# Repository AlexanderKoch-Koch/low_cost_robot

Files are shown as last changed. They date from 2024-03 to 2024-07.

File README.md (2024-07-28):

# Low-Cost Robot Arm
Join the waitlist here to get all the parts in one package: https://tau-robotics.com/robots

This repository contains the files to build and control a low-cost robot arm that costs about $250. You can also build a second robot arm (the leader arm) to control the other arm (the follower arm) that costs about $180, for a total of $430. The design of the leader is inspired by the [GELLO project](https://github.com/wuphilipp/gello_mechanical) but is simpler to build. Such a robot arm is well suited for [robot learning](https://x.com/alexkoch_ai/status/1756500716854841835?s=20). Two of those arms are also capable of [folding clothes](https://x.com/alexkoch_ai/status/1772750496174149708?s=20).

This robot arm uses Dynamixel XL430 and Dynamixel XL330 servo motors. The XL430 motors are almost twice as strong and are used for the first two joints.
The XL330 motors are weaker but weigh only 18g each. This makes the arm very lightweight and fast.
Dynamixel sells the U2D2 adapter to connect the servos to a computer. However, this is very expensive and the latency is very high. This build uses another cheaper adapter board instead.
The robot arm can be controlled with the Dynamixel SDK: ```pip install dynamixel-sdk```

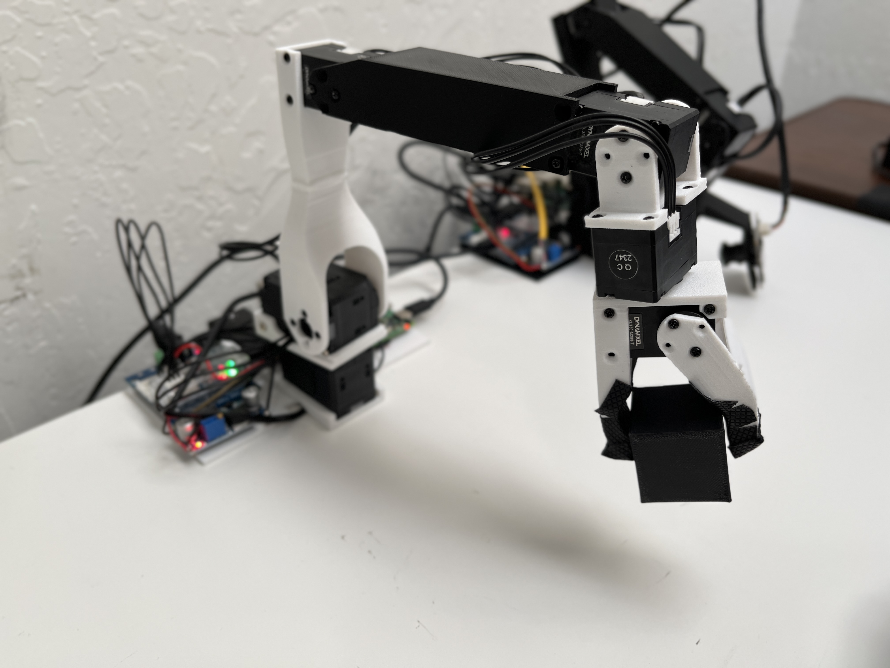
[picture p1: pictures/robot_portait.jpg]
Robot Arm


## Follower Arm

### Required Materials

| Part | Cost | Buying link | Specs |
|---|---|---| --- |
| 2x Dynamixel XL430-W250 | $100 | https://www.robotis.us/dynamixel-xl430-w250-t/ | https://emanual.robotis.com/docs/en/dxl/x/xl430-w250/ |
| 4x Dynamixel XL330-M288 | $96  | https://www.robotis.us/dynamixel-xl330-m288-t/ | https://emanual.robotis.com/docs/en/dxl/x/xl330-m288/|
| XL330 Idler Wheel | $10  | https://www.robotis.us/fpx330-h101-4pcs-set/ | **Note**: pack of four; three needed for  longer version pictured above (with elbow-to-wrist extension), two needed for shorter version shown in the [assembly video](https://youtu.be/RckrXOEoWrk)|
| XL430 Idler Wheel | $7 | https://www.robotis.us/hn11-i101-set/ | |
| Waveshare Serial Bus Servo Driver Board | $10  | https://a.co/d/7C3RUYU | |
| Voltage Reducer | $10 | https://a.co/d/cy02ADW | **Note**: pack of six, only one needed per follower arm |
| 12V Power Supply | $12  | https://a.co/d/40o8uMN | |
| Table Clamp | $6 | https://a.co/d/4KEiYdV | |
| Wires | $7 | https://a.co/d/hQfk2cb | |
| Total | $258 | | |

There is usually a 10% discount code for the Robotis shop. It might also help to add some grip tape to the gripper (e.g. https://a.co/d/dW7BnEN). A USB-C cable is necessary to connect the servo driver board to a computer.

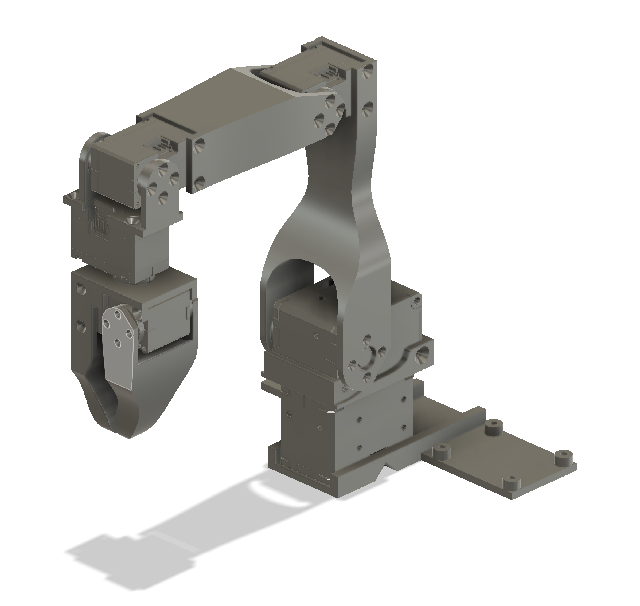
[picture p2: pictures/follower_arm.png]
follower


### Assembly

Video of the assembly: https://youtu.be/RckrXOEoWrk

1. Print all parts with a 3D printer
   1. The STL files are in `hardware/follower/stl`
   2. The parts are designed to be easy to print; only the moving part of the gripper needs supports
2. Scanning motors
   1. Connect the driver board to a computer (should work with Linux and MacOS)
   2. Figure out the device name (e.g. tty.usbmodem57380045631 for MacOS): ```ls /dev/tty.*```
   3. Scan each motor individually with [Dynamixel Wizard](https://emanual.robotis.com/docs/en/software/dynamixel/dynamixel_wizard2/)
      1. Set the baudrate to 1M for all motors
      2. Set the servo IDs to 1 for the shoulder to 5 (6 if using the elbow-to-wrist extension) for the gripper servo
3. Assembly
   1. Assemble the arm without the base
      1. Make sure that the servos are fixed in the same position as in the CAD
      2. The servo horn should be in the default position when screwed in
   2. Solder wires onto voltage reducer; input should be connected to female connectors and the output to male connectors
   3. Screw the voltage reducer and the servo driver board onto the base
   4. Screw the base onto the arm
   5. Connect D, V, and G ports on the driver board to the shoulder rotation servo
   6. Connect the shoulder rotation servo to the shoulder lift servo
   7. Connect the input for the voltage reducer to V and G ports on the driver board
   8. Connect the output of the voltage reducer and the remaining D port of the driver board to the elbow servo
   9. Connect the driver board to the power supply
   10. Connect to an XL330 servo and view the input voltage on Dynamixel Wizard, then adjust the screw on the voltage reducer until the input voltage is 5V

## Leader Arm

### Required Materials

| Part | Cost | Buying link | Specs |
|---|---| --- | --- |
| 6x Dynamixel XL330-M077 | $144 |  https://www.robotis.us/dynamixel-xl330-m077-t/ | https://emanual.robotis.com/docs/en/dxl/x/xl330-m077/|
| XL330 Frame | $7 | https://www.robotis.us/fpx330-s101-4pcs-set/ | |
| XL330 Idler Wheel | $10  | https://www.robotis.us/fpx330-h101-4pcs-set/ | **Note**: pack of four; three needed for longer version (with elbow-to-wrist extension), two needed for shorter version pictured below |
| Waveshare Serial Bus Servo Driver Board | $10  | https://a.co/d/7C3RUYU | |
| 5V Power Supply | $6 | https://a.co/d/5u90NVp | |
| Table Clamp | $6 | https://a.co/d/4KEiYdV | |
| Total | $183 | | |

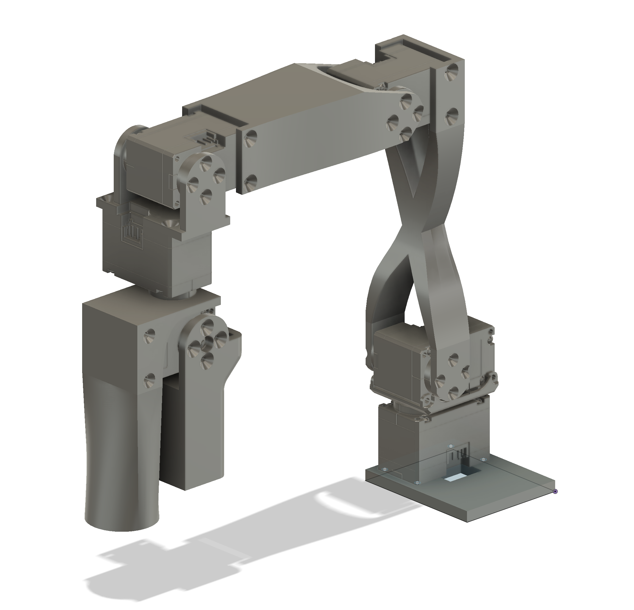
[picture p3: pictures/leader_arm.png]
leader


### Assembly

The assembly of the leader arm is simpler since all motors use 5V. The gripper is replace by a handle and a trigger. During use, a small torque can be applied to the trigger so that it opens by default. The GELLO design uses a spring for this purpose but it is much more difficult to assemble.
The `teleoperation.py` script can be used to test the arms. However, the device names might have to be adjusted.

## Simulation
A basic simulation environment in MuJoCo is available by running `simulation.py`.

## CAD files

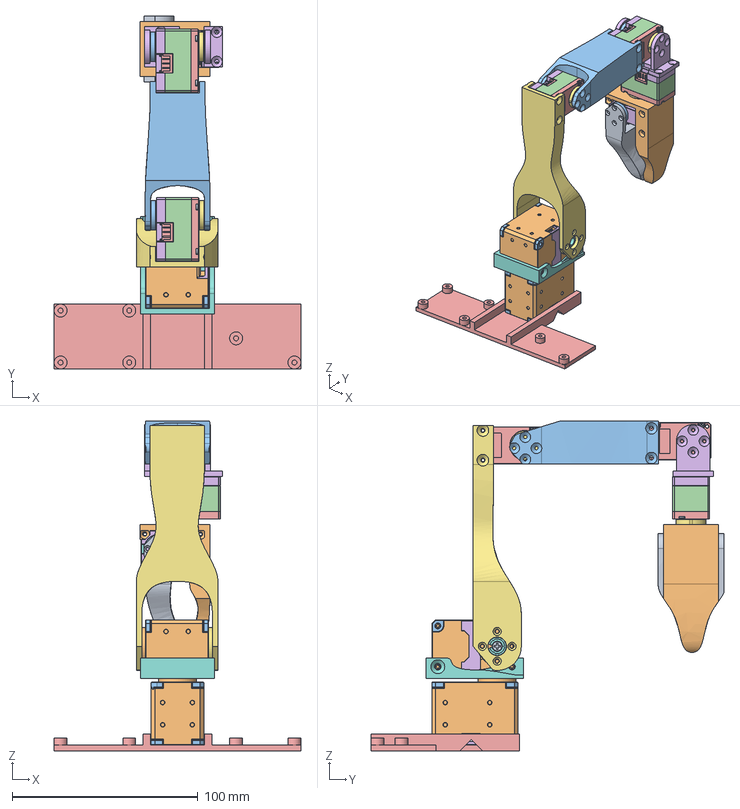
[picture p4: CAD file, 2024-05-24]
hardware/follower/step/arm.step
133.0 x 190.2 x 177.6 mm
DC11_A01_DUMMY x 2
DX124_SCREW-COVER x 2
B3B-EH x 4
DC11_A01_CASE_CVR_DUMMY x 2
DC11_A01_IDLER_DUMMY x 2
DC11_A01_IDLER_CAP_DUMMY x 2
DC11_A01_IDLER_SCREW x 2
FHS_M2_5X10 x 16
DC11_A01_SPACER_DUMMY x 16
DC15_A01_CASE_M_DUMMY x 4
DC15_A01_CASE_F_DUMMY x 4
DC15_A01_CASE_B_DUMMY x 4
DC15_A01_HORN_DUMMY x 4
DC15_A01_LED_CAP2_DUMMY x 4
PHS_1_7X20_5_DC10 x 16
BTS2_M2_6X8 x 8
DC15_A01_HORN_IDLE2_DUMMY x 4
DC15_A01_IDLE_CAP_DUMMY x 4
B3B-EH_1 x 8
Base
shoulder_rotation
connector
rotation connector
moving side
static side
connector_1

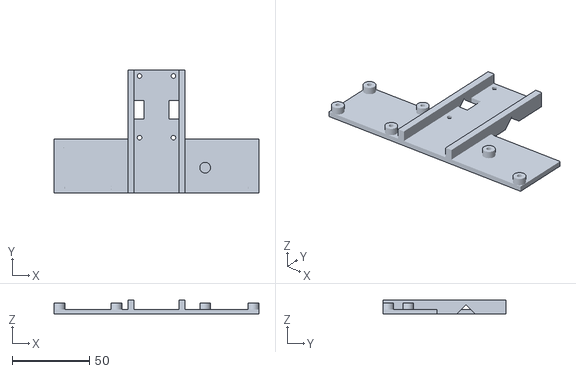
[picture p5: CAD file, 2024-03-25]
hardware/follower/stl/base.stl
133.0 x 80.0 x 9.00

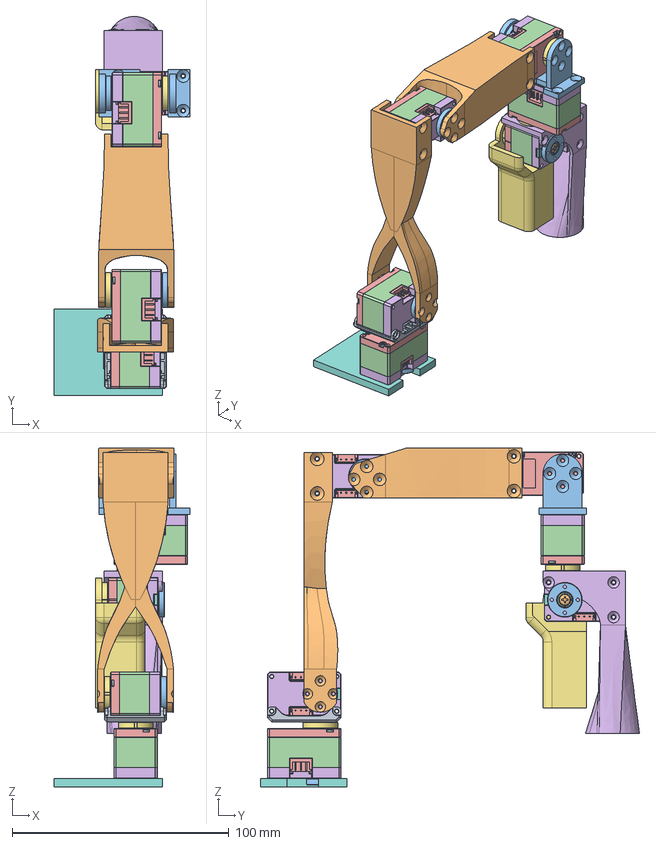
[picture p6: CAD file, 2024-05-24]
hardware/leader/step/leader_arm.step
62.7 x 175.0 x 156.5 mm
Servo Connector redesign
shoulder_rotation
DC15_A01_CASE_M_DUMMY x 6
DC15_A01_CASE_F_DUMMY x 6
DC15_A01_CASE_B_DUMMY x 6
DC15_A01_HORN_DUMMY x 6
DC15_A01_LED_CAP2_DUMMY x 6
PHS_1_7X20_5_DC10 x 24
BTS2_M2_6X8 x 12
DC15_A01_HORN_IDLE2_DUMMY x 6
DC15_A01_IDLE_CAP_DUMMY x 6
B3B-EH x 12
handle
trigger
base
fpx330-s101
connector

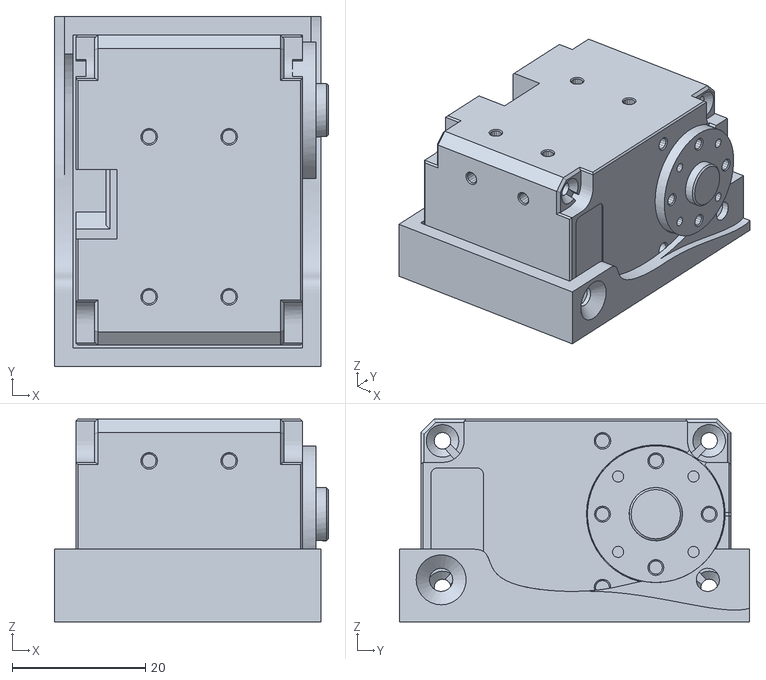
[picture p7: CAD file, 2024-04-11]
simulation/low_cost_robot/assets/first-bracket-motor_1.stl
41.1 x 52.5 x 30.4

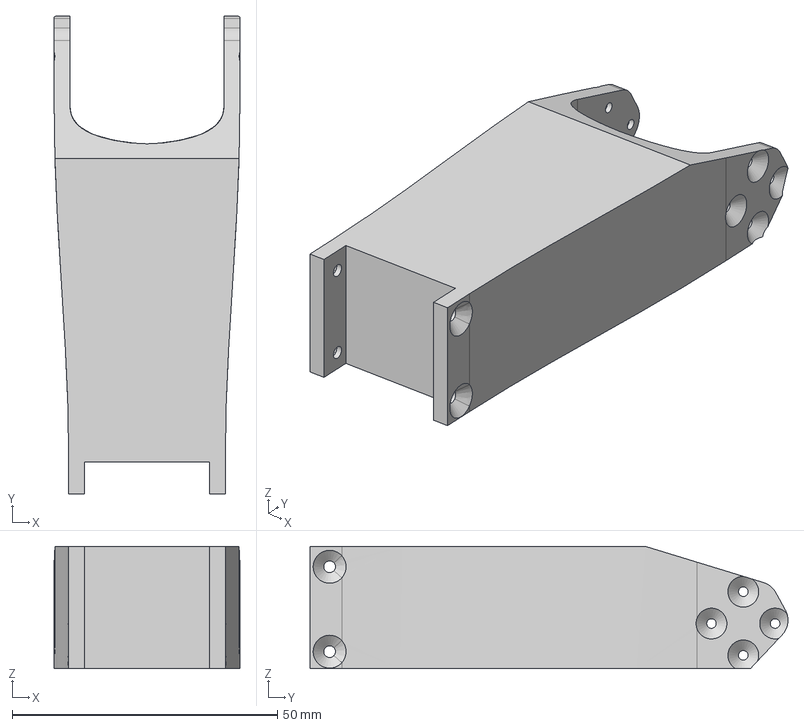
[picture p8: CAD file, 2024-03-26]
hardware/follower/step/elbow_to_wrist_extension.step
35.0 x 90.1 x 23.0 mm

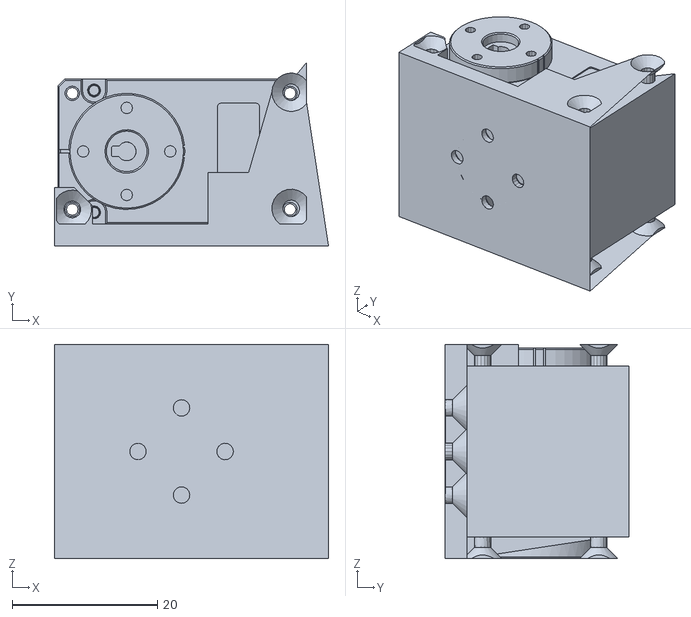
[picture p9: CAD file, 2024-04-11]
simulation/low_cost_robot/assets/gripper-static-motor-pt1.stl
37.8 x 25.3 x 29.5

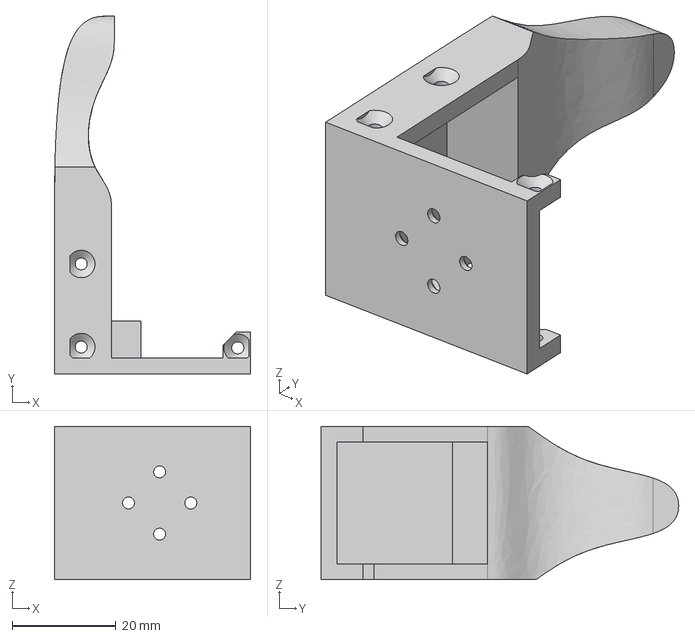
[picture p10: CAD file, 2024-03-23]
hardware/follower/step/gripper_static_part.step
37.7 x 68.9 x 29.5 mm

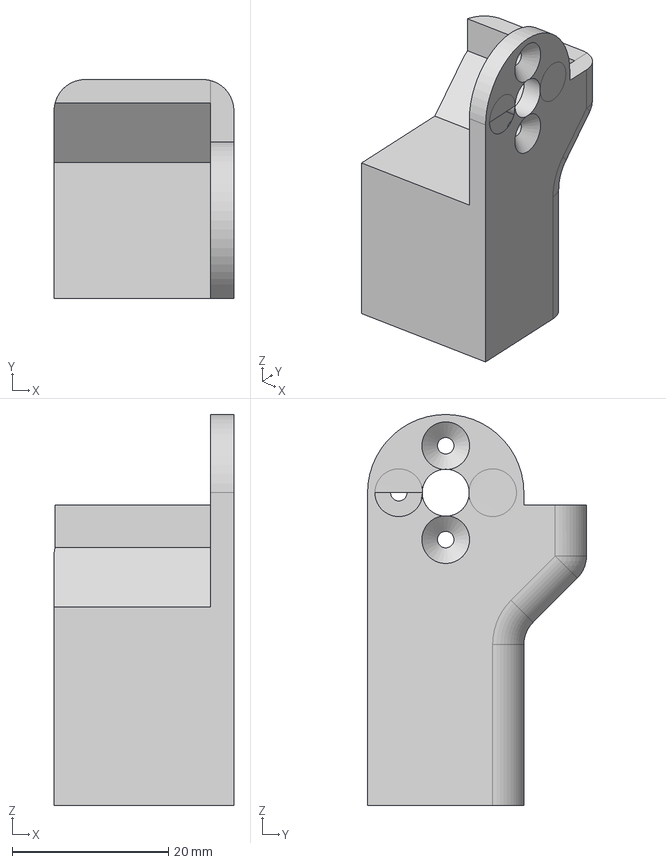
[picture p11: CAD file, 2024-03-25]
hardware/leader/step/gripper_trigger.step
23.0 x 28.0 x 50.0 mm

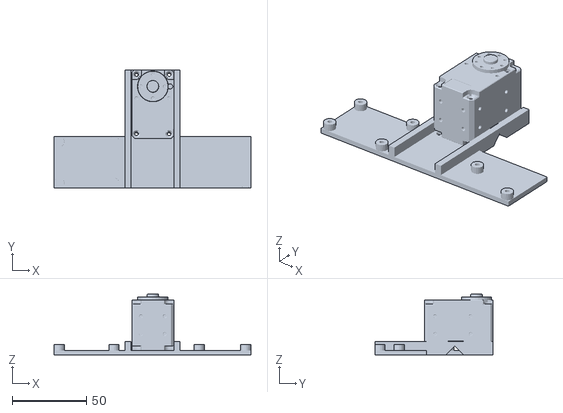
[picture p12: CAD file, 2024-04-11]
simulation/low_cost_robot/assets/base_link.stl
133.0 x 80.0 x 40.9

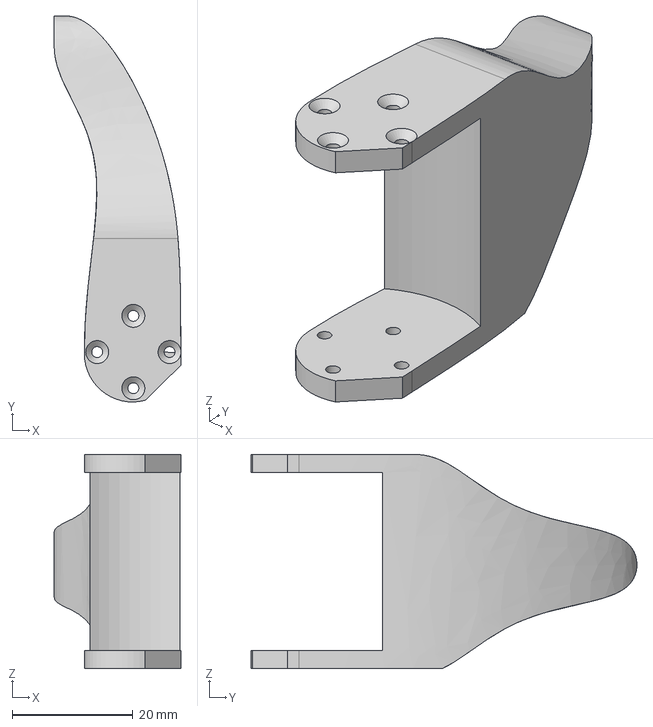
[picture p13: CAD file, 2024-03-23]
hardware/follower/step/gripper_moving_part.step
21.0 x 64.0 x 35.5 mm

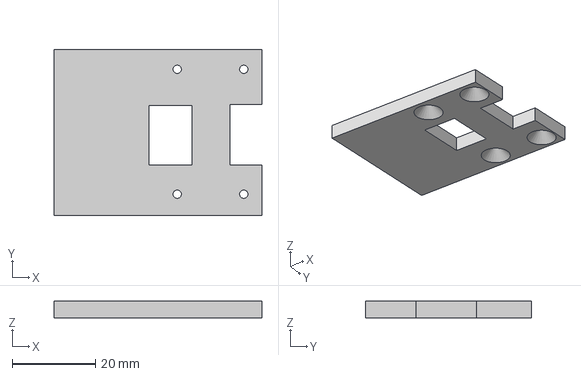
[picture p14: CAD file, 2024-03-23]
hardware/leader/step/base.step
50.0 x 40.0 x 4.00 mm

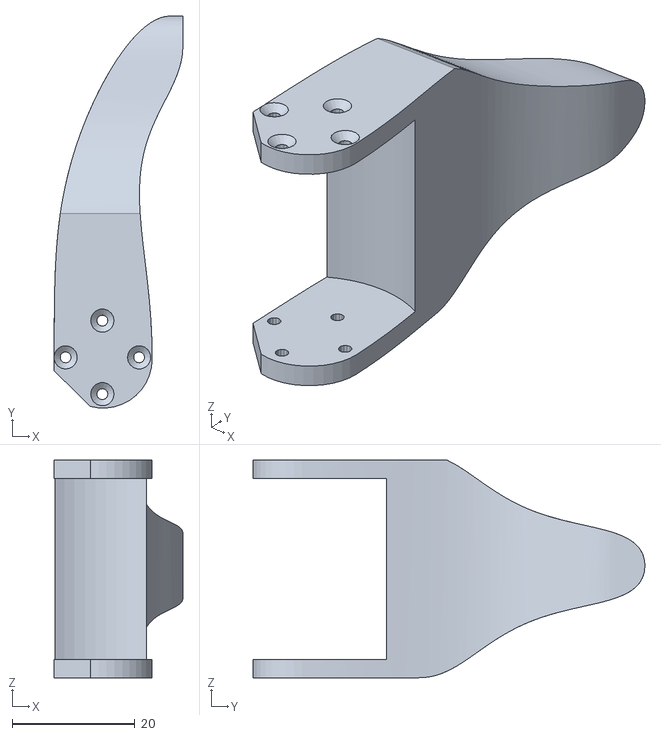
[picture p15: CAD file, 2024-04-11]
simulation/low_cost_robot/assets/gripper-moving-part-dumb_v2_1.stl
21.0 x 64.0 x 35.5

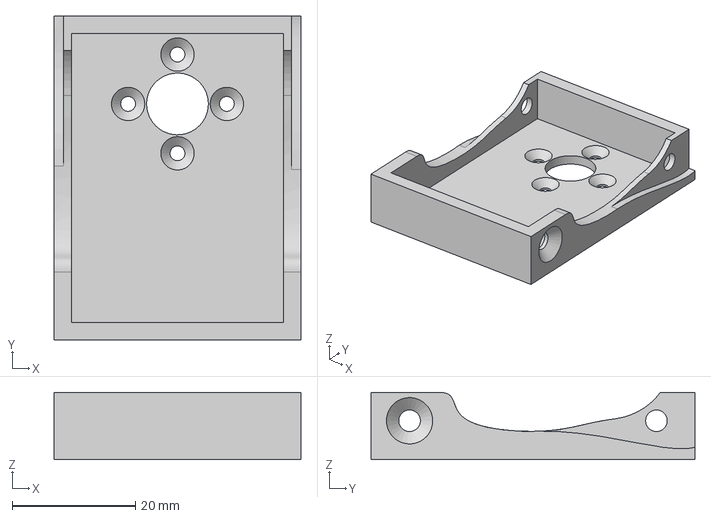
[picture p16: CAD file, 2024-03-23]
hardware/follower/step/shoulder_rotation.step
40.0 x 52.5 x 10.9 mm

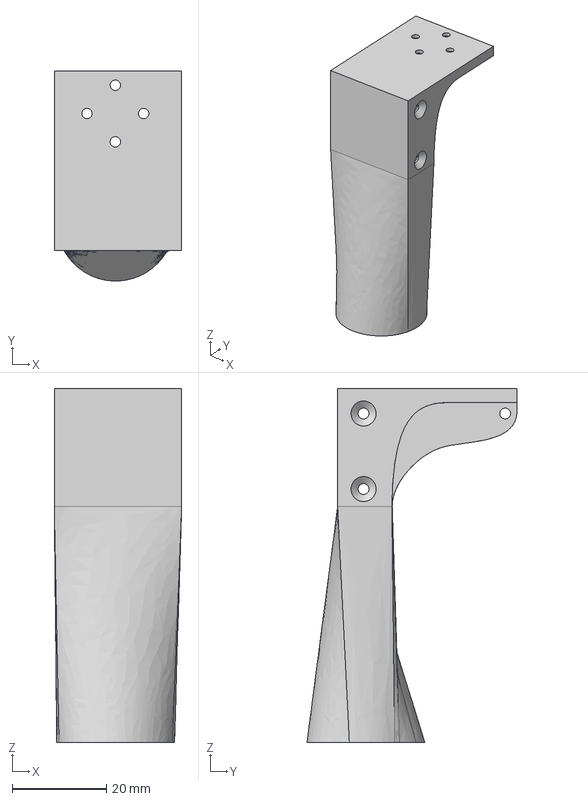
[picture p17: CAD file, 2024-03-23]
hardware/leader/step/gripper_handle.step
27.0 x 44.5 x 75.0 mm

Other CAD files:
simulation/low_cost_robot/assets/elbow-to-wrist-motor-reference_v1_1.stl
hardware/follower/step/elbow_to_wrist.step
hardware/leader/step/elbow_to_wrist.step
hardware/follower/follower_arm.f3z
hardware/follower/step/shoulder_to_elbow.step
hardware/follower/stl/elbow_to_wrist.stl
hardware/follower/stl/elbow_to_wrist_extension.stl
hardware/follower/stl/gripper_moving_part.stl
hardware/follower/stl/gripper_static_part.stl
hardware/follower/stl/shoulder_rotation.stl
hardware/follower/stl/shoulder_to_elbow.stl
hardware/leader/leader_arm.f3z
hardware/leader/step/shoulder_to_elbow.step
hardware/leader/stl/base.stl
hardware/leader/stl/elbow_to_wrist.stl
hardware/leader/stl/elbow_to_wrist_extension.stl
hardware/leader/stl/gripper_handle.stl
hardware/leader/stl/gripper_trigger.stl
hardware/leader/stl/shoulder_to_elbow.stl
simulation/low_cost_robot/assets/gripper-static-motor-pt2.stl
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

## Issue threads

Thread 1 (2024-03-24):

Smaller servos are unclear

thomwolf, 2024-03-24:
Hi, thanks a lot for the amazing project.

Just a note that in the table you indicate conflicting references for the smaller motors:

---

3x Dynamixel xl330-w280
$72	https://www.robotis.us/dynamixel-xl330-m077-t/
https://emanual.robotis.com/docs/en/dxl/x/xl330-m288/

---

It's more a "M" than a "W" and probably more a m077 than a m288 I guess

AlexanderKoch-Koch, 2024-03-24:
Thank you. I've fixed it now. It should be Dynamixel xl330-m288 with higher torque for the follower and Dynamixel xl330-w077 for the leader arm.

Closed 2024-03-24.

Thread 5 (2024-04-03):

Trying to figure out if wrist is supposed to be rotatable during assembly

moaazsidat, 2024-04-03:
I'm trying to figure if the wrist is supposed to be rotatable during the assembly since I didn't quite catch that from the youtube video.

Are the screws here correct in being at the top and bottom, or do they need to be left and right?

I'm unable to rotate the wrist joint during assembly whereas all the other ones are rotatable by hand, is that expected?

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

AlexanderKoch-Koch, 2024-04-04:
I think the screws you used might be too long and block the rotation. You have to use the shortest screws here. You can just put in all four screws. I put in only two since it's faster and strong enough usually.

moaazsidat, 2024-04-04:
Ok, that was probably it, used smaller screws and applied a bit more force on manual rotation and that seemed to get it goin. It still seems a little frictiony on the rotation, so I might have gotten a bad servo.

Closed 2024-04-04.

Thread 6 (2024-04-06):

Longer servo connector

trzy, 2024-04-06:
Hi Alexander, thank you for open sourcing this. I printed out the components and noticed that there is a longer connector piece that would replace the component labeled "servo connector angle v1:1". I printed it too dense, so I won't use it, but I am going to print a lighter version of it. I see an even longer version in the photograph in the README.md. Is there any major disadvantage to using these longer versions? I assume you shortened it for stability purposes?

Some explanation of the discrepancy on the README would be very helpful for novices like myself.

Thank you!

AlexanderKoch-Koch, 2024-04-06:
It would not replace the "servo connector angle". You could use both to get a 5dof arm. The length of it does not really matter. A longer piece gives you a larger reach but is more difficult to control. I think the version in this repo has a good size.

trzy, 2024-04-07:
I see now looking more closely at the videos. This makes sense! Thank you. I've gotten the 4dof version built and working!

Closed 2024-04-07.

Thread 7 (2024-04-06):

How do you wire the leader arm + where does the 6th servo go?

ControlCplusControlV, 2024-04-06:
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
I've assembled the leader arm, but while the README calls for 6 servo motors I only ended up using 5? And I think I assembled it correctly? Also how does the wiring work for the leader arm, not sure how to do that, I'm guessing loosely like the follower but idk specifics.

Thanks for open-sourcing though! Looks sick and can't wait to try it out

ControlCplusControlV, 2024-04-06:
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
So it seems like that `extra` arm piece goes in the middle of that top segment? I don't think the images in the README show that, although it is in the stl files

AlexanderKoch-Koch, 2024-04-06:
You can use it with either five or six servos. The elbow_to_wrist_extension is the additional part. I designed it originally with only five servos. That's why the readme renders show only five servos.

ControlCplusControlV, 2024-04-06:
Ah I see, thanks! I did manage to get it working with the elbow_to_wrist_extension just now. Do you have a wiring diagram or more clear pictures on how to wire the leader arm? Not sure how I should set it up

AlexanderKoch-Koch, 2024-04-06:
The wiring for the leader arm is simpler. You can directly connect the servo control board to the first servo motor and then daisy chain all the others since all servos in the leader arm use 5v.

ControlCplusControlV, 2024-04-06:
Oh I see, works great, thanks!

Closed 2024-04-06.

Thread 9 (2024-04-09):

What is the load capacity of this robotic arm?

heroacool, 2024-04-09:
@AlexanderKoch-Koch Thank you for sharing; this is a great project.
I'm curious about the maximum load capacity of this robotic arm, as it would help in assessing what kind of tasks the arm can perform.

AlexanderKoch-Koch, 2024-04-09:
For the four-axis version, it's a few hundred grams. I've posted a video with a heavier object here: https://x.com/alexkoch_ai/status/1771649728129687789. The payload of the five-axis arm at full extension is close to zero.

Closed 2024-04-13.

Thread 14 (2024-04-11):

Any ideas on how to debug flakey dynamixel connections?

moaazsidat, 2024-04-11:
Having trouble consistently being able to connect to motors and scan them via dynamixel, wondering if there's ways to debug it more

* When attaching them one by one, it works _most_ of the times, and nothing shows up on scanning via Dynamixel wizard rest of the time
* When trying to connect one motor to another, nothing shows up on scanning via Dynamixel wizard 100% of the time
* When have the whole setup wired, the smaller motors are blinking red (seems like that's incorrect voltage error) – and nothing shows up on Dynamixel wizard scanning

AlexanderKoch-Koch, 2024-04-11:
The Dynamixel wizard shows you the input voltage. You could check that this is correct. Otherwise, I have no idea.

moaazsidat, 2024-04-11:
Gotcha, will debug more, thanks!

Closed 2024-04-11.

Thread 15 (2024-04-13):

Might want to recommend a different way to set the voltage

johnowhitaker, 2024-04-13:
"Connect to an XL330 servo and view the input voltage on Dynamixel Wizard, then adjust the screw on the voltage reducer until the input voltage is 5V"

My voltage reducers came set such that the output was 12V and needed many turns of the pot to start bringing that down, by which time the poor little servo had let the magic smoke out. Might have been user error my side but for my second attempt I used a PC fan instead, which was happy with 12V input until I had time to set the output voltage down to 5V.

AlexanderKoch-Koch, 2024-04-13:
Interesting. I haven't been able to destroy a servo this way. Are you sure it's dead? There is a recovery feature in the Dynamixel Wizard.

johnowhitaker, 2024-04-13:
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
Burnt beyond recovery 😂 There's a small chance I had wires switched but I'm too chicken to try on another servo to find out. Possibly also caused by connecting the servo *after* power and USB?

karanchahal, 2025-01-13:
Yeah the instructions are pretty vague, the issue is the dynamixel motors dont clearly specify what is ground, + and -ve in their diagram.

I think we might be doing it wrong, plus the instructions have some sort of magicness to them.

Connect the D and G to the voltage reducer ? WHy, I would expect Ground to be untouched and simply attached to ground of the servo.

And the V and D (+ve and -ve) to be atatched to the voltage reducer and hooked up the + and -ve of the servo.

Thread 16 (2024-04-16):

Apple Slilicon Issues with Dynamixel Wizard

ControlCplusControlV, 2024-04-16:
Is there any way around Dynamixel wizard? I'm on M1 Apple Silicon, and the App Store installation like they suggest does not work, Dynamixel wizard either doesn't detect the motors (usb c into the servo board for the 6v motor, attempting to scan with jumper wires into the motor, tried both orientations, tried with additional dc power, and without (on the other port) and it either won't detect the motor at all, or it will detect a motor on every single id, not sure what to do, appreciate any advice and can close if its not relevant

edward-io, 2024-04-16:
I have an M1 max macbook pro, and the Dynamixel Wizard worked fine when using the Waveshare board on both dynamixels servos when powered with 6v DC. Are you identifying the motors one at a time?

LouisFoucard, 2024-04-23:
Did you figure out the issue? I am also having trouble with the Dynamixel wizard, on Linux. Installed Dynamixel_sdk, followed the steps in https://emanual.robotis.com/docs/en/software/dynamixel/dynamixel_wizard2/#basic-features to install the wizard, but the scan does not find any connected motors. I am powering the board with 12v, and I see the XL430 blink once red, so seems to be powered correctly, and I can see the board connected at '/dev/ttyACM0'.
I also tried running the `ping.py` from dynamixel sdk, its able to open the port and change the baudrate, but getting no status packet from the XL430.
```
Succeeded to open the port
Succeeded to change the baudrate
[TxRxResult] There is no status packet!
```

LouisFoucard, 2024-04-23:
started a thread in robotis' forum to https://forum.robotis.com/t/dynamixel-not-seeing-any-device/5697

LouisFoucard, 2024-04-25:
Finally got it to work: it was a bad board. Ordered another waveshare controller and everything worked fine. They seem to have a pretty high rate of failure, but even if you have to buy 2 its still cheaper than the u2d2..

peeeanut, 2024-04-29:
Can you show me your wires? I have the same issue as you.

LouisFoucard, 2024-05-01:
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

LouisFoucard, 2024-05-01:
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

Make sure you try a couple of these waveshare boards though, I think a lot of them aren't working

beduffy, 2024-05-05:
I think I have the same problem but not sure, I'm on ubuntu and not detecting anything in dynamixel wizard but also not getting scenario of robot on all IDs. I sometimes get a faint red light on the dynamixel which soon after disappears but find it hard to reproduce this light.

Initially, I want to control just 1 dynamixel servo, therefore I won't have the yellow wire going into D in the above diagram. @LouisFoucard do you think I will be able to control just 1 XL330-M288 this way or is the yellow wire needed for powering the daisychain with waveshare? I will order a 2nd dynamixel in case this is needed. Also considering ordering another waveshare or even the U2D2.

LouisFoucard, 2024-05-06:
For just testing one of the base motors you don't need the yellow data wire (nor the other 2 power wires since the base and shoulder motors get their power directly from the wave share board).
The faint red light is expected, it's just the motor turning on. If it blinks it means the input voltage is too high.

Most likely though you have a faulty waveshare board (if nothing works after checking all wires). My board was faulty and at least one other person also had a faulty board.

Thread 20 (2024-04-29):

How do you control the robot arm?

johnnevins, 2024-04-29:
Hi, thanks much for sharing this low-cost solution and saw your demo video on X which is great.
Wonder did you use a local PC with GPU to implement the inference of imitation learning? Would it be possible to use a remote server with GPU to control the arm?
I've read through the readme, but not able to find how the algorithm communicates with the hardware, could you elaborate more on this?

Appreciated
Patrick

AlexanderKoch-Koch, 2024-04-29:
I've used my macbook directly to interface with the servos. In newer demos, I've used Raspberry Pis on the robot arms to connect them via ethernet to a central server.

johnnevins, 2024-04-30:
> I've used my macbook directly to interface with the servos. In newer demos, I've used Raspberry Pis on the robot arms to connect them via ethernet to a central server.

Thanks much for the reply, as for the Raspberry Pis& server combination you mentioned, how do you translate output of the algorithm(position control I guess?) to executable code for hardware? Do you use GPIO?

Bests:)

Closed 2024-09-10.

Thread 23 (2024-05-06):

on-wrist camera

lliuz, 2024-05-06:
Hi, thanks much for sharing this low-cost project.
Have you ever tried putting a on-wrist camera on the follow arm?
Can you provide some help about what the maximum weight the motor can support for a on-wrist camera and if there is an stl file for the relevant connector?

starjokers, 2024-05-16:
Hi，
Have you copy this arm? Do you have the training algorithm to fold the clothes? Thank you!

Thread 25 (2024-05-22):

The third servo cannot support the entire arm

starjokers, 2024-05-22:
Hi, thanks so much for sharing this low-cost project.
After assembling this 6-axis robotic arm, I found that the third servo lacks sufficient strength when controlling the arm, and it often errors out after a short period of operation. Is there any solution to this issue?
Thank you!

Qu3tzal, 2024-05-26:
It doesn't hold the arm in the right position? Is it a holding torque issue?

starjokers, 2024-05-27:
Maybe，it would not work after few operation. We should upluge the power to recovery it.

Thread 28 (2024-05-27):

关于Dynamixel XL330-M288的个数问题

dawangwhere, 2024-05-27:
你好，我看到你的组装视频里面用到Dynamixel XL330-M288的数量是3个，材料清单中却是4个，请问是怎么会事？

Leonmel, 2024-05-29:
hi @dawangwhere 你好，我想建一个中文的qq群来讨论关于 low_cost_robot 的开发，欢迎加入。群号 631386853

tc-huang, 2024-05-29:
Hi @dawangwhere,
Ｍaybe the closed issue #7 is related to your question.

@dawangwhere 你好，
或許已關閉的 issue #7 與你的問題有關。

Best regards,
tc-huang

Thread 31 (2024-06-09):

the 3D printed base for follower arm is not strong enough?

jimtangshfx, 2024-06-09:
Hi,
Thanks for sharing this project.
I Printed the base of follower arm and height of the bottom base is only around 3mm , so the one I printed out using PLA at infill 60% is very soft and weak, not strong enough. I wonder what material are you using and how come yours looks very strong?
Thank you.
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

AlexanderKoch-Koch, 2024-06-09:
I'm using standard PLA. When you use the table clamp to fix it to a table it becomes quite strong since you can put the clamp very close to the first servo motor.

jimtangshfx, 2024-06-09:
> I'm using standard PLA. When you use the table clamp to fix it to a table it becomes quite strong since you can put the clamp very close to the first servo motor.

Hi, Alex
Thanks for your quick reply. I wonder why my printed base is so weak that I can even bend it using my hand?
what's your infill percentage and wall thickness? I am using below settings.
Layer height: 0.3mm
Wall thickness: 0.8 mm
Top-bottom thickness: 1.1mm
Infill: 60% Grid

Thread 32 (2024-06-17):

URDF with extension?

Tianchong-Jiang, 2024-06-17:
Hi Alex,

I built a follower arm and it was really nice. Thanks for the great work!

I wonder if you have an URDF file for the follower arm with the extension?

I am also happy to add the extension to the URDF file myself. I've been editing the raw file and rendering the changes with rviz. It was difficult to align the axis of rotation and other stuff. What software have you been using to make the URDF file?

Thank you!

Best regards,
Tianchong Jiang

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

sinantie, 2024-06-18:
Hi Alex (and Tianchong),

This is an amazing project!
I have also built the follower and leader robots and tried to take a slightly different route. I have "updated" the Fusion follower_arm.f3z model (.f3z) instead with the elbow_to_wrist extension. I've been struggling a bit though to "export" to URDF... Trying to add the wrist extension within the MuJoCo visualiser by hand is quite hard, as it's a lot of guesswork to "nail" the `pos`.

I've tried exporting with the Fusion to URDF plugin, but it doesn't work "out of the box"  which makes me think that it was not what was originally used (as the plugin requires to follow a few naming/design conventions which doesn't seem to be the case with the .f3z model).

Any thoughts?

Thanks a lot!!

Cheers,

Yannis Konstas

tc-huang, 2024-06-19:
Hello @Tianchong-Jiang and @sinantie,

I have created PR #33, which includes the `URDF` for the follower arm, including the `elbow_to_wrist_extension` part.

I hope this will be helpful.

Best regards,
tc-huang

Tianchong-Jiang, 2024-06-20:
Hi @tc-huang,

Thank you so much for the file!

Best,
Tiachong

Closed 2024-06-20.

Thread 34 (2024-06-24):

Is it possible to avoid or replace HN11-I101 Set since it is out of stock?

ex3ndr, 2024-06-24:
Currently Robotis don't have them in stock and it seems they are almost single vendor that sells this part.

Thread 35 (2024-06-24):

There are no simulation for 6dof arm?

ex3ndr, 2024-06-24:
It seems it is missing and all code is implemented for 5dof variant.

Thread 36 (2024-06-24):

Waveshare board issue?

yudhisteer, 2024-06-24:
Hi,
I bought two waveshare board and when testing the motors, it is not being recognized. What is the probability that two of the waveshare board is not good?

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

ex3ndr, 2024-06-29:
You need to supply power to them to power up

MichaelrMentele, 2024-07-08:
I'm not seeing the motor either.
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

I do see the board:
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

But scan finds nothing. Tried two boards. Swapped the motors.

MichaelrMentele, 2024-07-09:
> Hi, I bought two waveshare board and when testing the motors, it is not being recognized. What is the probability that two of the waveshare board is not good?

It looks like you can detect the motor when doing the firmware updates though based on your screenshot?

MichaelrMentele, 2024-07-09:
For me it's definitely the power supply. The 5v won't power the 330 for more than a moment. The 12 v causes the 330 to burn up but won't power the 430 for more than a moment.

MichaelrMentele, 2024-07-17:
@yudhisteer any update?

MichaelrMentele, 2024-08-13:
I had one bad board -- got a new one and it worked. Makes you want to just use the U2D2

karanchahal, 2025-01-13:
Yeah for sure, U2D2 would have helped I think. But now I am in too deep, I burnt 2 waveshares in this process.

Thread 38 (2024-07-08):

Waveshare connector doesn't fit the servo wire

MichaelrMentele, 2024-07-08:
The connectors do not fit together. If this is expected it would be good to extend the instruction to trim the connector.

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

MichaelrMentele, 2024-07-08:
Highly likely I am confused -- unfamiliar with all this. Going off of the dynamixel quickstart example. https://www.youtube.com/watch?v=JRRZW_l1V-U

Screenshots for each step would be great.

MichaelrMentele, 2024-07-17:
I ended up clipping off the outter edge but can't seem to keep motors powered.

moaazsidat, 2024-08-02:
@MichaelrMentele you'll need male-female jumper wires to connect these

meetsitaram, 2024-08-18:
I used extra wires to connect it this way.
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

karanchahal, 2025-01-13:
What is +ve, -ve and GND on the white connector of the dynamixel ?

I think the D, V and G in the waveshare means.
-ve, +ve and ground

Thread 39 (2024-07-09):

Linked Power Supplies Don't Power their Respective Motors

MichaelrMentele, 2024-07-09:
When I use the 5v adapter it doesn't power the 330's for more than a brief moment on plug in.

When I use the 12v the motor it powers the 330's but starts to burn up as @jzxchiang1 experienced in #26

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

catid, 2024-07-12:
You might have the cables in the wrong places.  Use the male/female jumper wires to swap them

MichaelrMentele, 2024-07-17:
Thanks Chris but I've flipped the jumper end orientation but it doesn't make a difference. Do you have a screenshot of your working board @catid? I wonder if my waveshare board is bad or was ruined during one of the permutations.

meetsitaram, 2024-08-18:
My waveshare board got ruined, most probably because i might have connected wrong wires. When i tried scanning for servos using the dynamizel wizard, i was getting a warning on windows saying it is unable to connect to the hardware properly. Had to order a new board.

karanchahal, 2025-01-13:
the 5v adapter will not help as the dc jack can only support 9-12 v

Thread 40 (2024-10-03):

Arm URDF is out-of-date (has 5 dofs)

samzapo, 2024-10-03:
The URDF for the arm is out of date.

While the images used in the repo README are of the newer 6-dof arm, e.g.:
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

the URDF at `simulation/low_cost_robot/low-cost-arm.urdf` is of the older 5-dof arm, e.g.:
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

I've made an SDF of the new arm that may resolve this issue:
https://github.com/samzapo/gym-drake-lca/blob/main/gym_drake_lca/assets/follower_arm.sdf
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

reedscot, 2024-11-24:
I have a PR that adds simulation for the 6-DoF arm: https://github.com/AlexanderKoch-Koch/low_cost_robot/pull/41.

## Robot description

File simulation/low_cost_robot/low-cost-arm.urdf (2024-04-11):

<?xml version="1.0" ?>
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
<robot name="low-cost-arm">
  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
  <link name="base_link">
    <inertial>
      <origin rpy="0 0 0" xyz="-1.6196165020213455e-05 0.04676572591178276 0.014449624355634582"/>
      <mass value="0.06752363433035656"/>
      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
    </inertial>
    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
  </link>
  <link name="first-bracket-motor_1">
    <inertial>
      <origin rpy="0 0 0" xyz="0.0011215335520915035 -0.011960095984038348 0.012424221873872536"/>
      <mass value="0.050669759178187244"/>
      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
    </inertial>
    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
  </link>
  <link name="shoulder-to-elbow-motor_v1_1">
    <inertial>
      <origin rpy="0 0 0" xyz="-0.0191542760740305 -0.0012683813577475112 0.07144141167892787"/>
      <mass value="0.05261369068977079"/>
      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
    </inertial>
    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
  </link>
  <link name="elbow-to-wrist-motor-reference_v1_1">
    <inertial>
      <origin rpy="0 0 0" xyz="0.01951468809363352 0.026076660011439212 2.3261768583027198e-05"/>
      <mass value="0.02059907441055582"/>
      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
    </inertial>
    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
  </link>
  <link name="gripper-static-motor_v2_1">
    <inertial>
      <origin rpy="0 0 0" xyz="0.005421565533833407 0.019034667992307075 0.00011281388318701291"/>
      <mass value="0.030801959916802346"/>
      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
    </inertial>
    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
  </link>
  <link name="gripper-moving-part-dumb_v2_1">
    <inertial>
      <origin rpy="0 0 0" xyz="0.001094897934895013 0.025115003984107043 -0.01445125352746443"/>
      <mass value="0.013583445641331692"/>
      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
    </inertial>
    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
  </link>
  <joint name="Revolute 2" type="continuous">
    <origin rpy="0 0 0" xyz="0.00025 0.06875 0.0409"/>
    <parent link="base_link"/>
    <child link="first-bracket-motor_1"/>
    <axis xyz="0.0 0.0 1.0"/>
  </joint>
  <joint name="Revolute 3" type="continuous">
    <origin rpy="0 0 0" xyz="0.0192 0.0002 0.01425"/>
    <parent link="first-bracket-motor_1"/>
    <child link="shoulder-to-elbow-motor_v1_1"/>
    <axis xyz="1.0 0.0 0.0"/>
  </joint>
  <joint name="Revolute 5" type="continuous">
    <origin rpy="0 0 0" xyz="-0.03375 0.0148 0.1083"/>
    <parent link="shoulder-to-elbow-motor_v1_1"/>
    <child link="elbow-to-wrist-motor-reference_v1_1"/>
    <axis xyz="1.0 -0.0 0.0"/>
  </joint>
  <joint name="Revolute 6" type="continuous">
    <origin rpy="0 0 0" xyz="0.013407 0.044938 -1.3e-05"/>
    <parent link="elbow-to-wrist-motor-reference_v1_1"/>
    <child link="gripper-static-motor_v2_1"/>
    <axis xyz="-0.0 -1.0 0.0"/>
  </joint>
  <joint name="Revolute 7" type="continuous">
    <origin rpy="0 0 0" xyz="-0.00755 0.01299 0.01425"/>
    <parent link="gripper-static-motor_v2_1"/>
    <child link="gripper-moving-part-dumb_v2_1"/>
    <axis xyz="-0.0 -0.0 -1.0"/>
  </joint>
</robot>

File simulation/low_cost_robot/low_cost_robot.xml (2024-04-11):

<mujoco model="low_cost_robot">
    <compiler angle="radian" meshdir="assets" texturedir="assets" autolimits="true"/>
    <!-- The timestep has a big influence on the contacts stability -->
    <option cone="elliptic" impratio="10" timestep="0.001"/>

    <asset>
        <mesh file="base_link.stl" scale="0.001 0.001 0.001"/>
        <mesh file="first-bracket-motor_1.stl" scale="0.001 0.001 0.001"/>
        <mesh file="shoulder-to-elbow-motor_v1_1.stl" scale="0.001 0.001 0.001"/>
        <mesh file="elbow-to-wrist-motor-reference_v1_1.stl" scale="0.001 0.001 0.001"/>
        <mesh file="gripper-static-motor-pt1.stl" scale="0.001 0.001 0.001"/>
        <mesh file="gripper-static-motor-pt2.stl" scale="0.001 0.001 0.001"/>
        <mesh file="gripper-moving-part-dumb_v2_1.stl" scale="0.001 0.001 0.001"/>
    </asset>

    <default>
        <default class="low_cost_robot">
            <general biastype="affine"/>
            <!-- NOTE: the joint pos are defined in world frame, so they're built by summing over urdf relative joint positioning -->
            <!-- NOTE: values other than axis and pos here have not been properly identified -->
            <joint axis="0 1 0"/>
            <default class="joint1">
                <joint axis="0 0 1" pos="0.00025 0.06875 0.0409" range="-3.14158 3.14158" damping="0.1"/>
                <position ctrlrange="-3.14158 3.14158" kp="25"/>
            </default>
            <default class="joint2">
                <joint axis="1 0 0" pos="0.01945 0.06895 0.05515" range="-3.14158 3.14158" damping="0.1"/>
                <position ctrlrange="-3.14158 3.14158" kp="25"/>
            </default>
            <default class="joint3">
                <joint axis="1 0 0" pos="-0.0143 0.08375 0.16345" range="-3.14158 3.14158" damping="0.1"/>
                <position ctrlrange="-3.14158 3.14158" kp="25"/>
            </default>
            <default class="joint4">
                <joint axis="0 -1 0" pos="-0.000893 0.128688 0.163437" range="-3.14158 3.14158" damping="0.1"/>
                <position ctrlrange="-3.14158 3.14158" kp="25"/>
            </default>
            <default class="joint5">
                <joint axis="0 0 -1" pos="-0.008443 0.141678 0.177687" range="-2.45 0.032" damping="0.1"/>
                <position ctrlrange="-2.45 0.032" kp="25"/>
            </default>
        </default>
    </default>

    <worldbody>
        <body name="base_link">
            <geom type="mesh" name="base_link" mesh="base_link" rgba="0.1 0.1 0.1 1"/>
            <body name="joint1">
                <joint name="joint1" class="joint1"/>
                <geom type="mesh" name="joint1" mesh="first-bracket-motor_1" rgba="0.1 0.1 0.1 1"/>
                <body name="joint2">
                    <joint name="joint2" class="joint2"/>
                    <geom type="mesh" name="joint2" mesh="shoulder-to-elbow-motor_v1_1" rgba="0.1 0.1 0.1 1"/>
                    <body name="joint3">
                        <joint name="joint3" class="joint3"/>
                        <geom type="mesh" name="joint3" mesh="elbow-to-wrist-motor-reference_v1_1" rgba="0.1 0.1 0.1 1"/>
                        <body name="joint4">
                            <joint name="joint4" class="joint4"/>
                            <geom type="mesh" name="joint4-pt1" mesh="gripper-static-motor-pt1" rgba="0.1 0.1 0.1 1"/>
                            <geom type="mesh" name="joint4" mesh="gripper-static-motor-pt2" rgba="0.1 0.1 0.1 1" contype="0" conaffinity="0"/>
                            
                            <!-- Rectangular pad for contact -->
                            <body name="joint4-pad">
                                <geom type="box" condim="3" friction="0.7" mass="0.01" solimp="0.95 0.99 0.001" solref="0.004 1" name="static_finger_pad" size="0.006 0.006 0.006" pos="0.0135 0.192 0.1635" priority="1" rgba="0 0 0 0"/>
                            </body>
                            
                            <body name="joint5">
                                <joint name="joint5" class="joint5"/>
                                <geom type="mesh" name="joint5" mesh="gripper-moving-part-dumb_v2_1" rgba="0.1 0.1 0.1 1" contype="0" conaffinity="0"/>
                                
                                <!-- Rectangular pad for contact -->
                                <body name="joint5-pad">
                                    <geom type="box" condim="3" friction="0.7" mass="0.01" solimp="0.95 0.99 0.001" solref="0.004 1" name="moving_finger_pad" size="0.006 0.006 0.006" pos="-0.0007 0.192 0.1635" euler="0 0 -0.3" priority="1" rgba="0 0 0 0"/>
                                </body>

                            </body>
                            <!-- End effector frame in the middle of the two grippers -->
                            <body>
                                <geom type="sphere" name="end_effector" size="0.001" pos="-0.005 0.1935 0.1635" contype="0" conaffinity="0" rgba="0 0 0 0"/>
                            </body>
                        </body>
                    </body>
                </body>
            </body>
        </body>
    </worldbody>

    <actuator>
        <position class="joint1" name="joint1" joint="joint1"/>
        <position class="joint2" name="joint2" joint="joint2"/>
        <position class="joint3" name="joint3" joint="joint3"/>
        <position class="joint4" name="joint4" joint="joint4"/>
        <position class="joint5" name="joint5" joint="joint5"/>
    </actuator>

</mujoco>

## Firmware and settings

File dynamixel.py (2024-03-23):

from __future__ import annotations
import math
import os
from dynamixel_sdk import *  # Uses Dynamixel SDK library
from dataclasses import dataclass
import enum


class ReadAttribute(enum.Enum):
    TEMPERATURE = 146
    VOLTAGE = 145
    VELOCITY = 128
    POSITION = 132
    CURRENT = 126
    PWM = 124
    HARDWARE_ERROR_STATUS = 70
    HOMING_OFFSET = 20
    BAUDRATE = 8


class OperatingMode(enum.Enum):
    VELOCITY = 1
    POSITION = 3
    CURRENT_CONTROLLED_POSITION = 5
    PWM = 16
    UNKNOWN = -1


class Dynamixel:
    ADDR_TORQUE_ENABLE = 64
    ADDR_GOAL_POSITION = 116
    ADDR_VELOCITY_LIMIT = 44
    ADDR_GOAL_PWM = 100
    OPERATING_MODE_ADDR = 11
    POSITION_I = 82
    POSITION_P = 84
    ADDR_ID = 7

    @dataclass
    class Config:
        def instantiate(self): return Dynamixel(self)

        baudrate: int = 57600
        protocol_version: float = 2.0
        device_name: str = ''  # /dev/tty.usbserial-1120'
        dynamixel_id: int = 1

    def __init__(self, config: Config):
        self.config = config
        self.connect()

    def connect(self):
        if self.config.device_name == '':
            for port_name in os.listdir('/dev'):
                if 'ttyUSB' in port_name or 'ttyACM' in port_name:
                    self.config.device_name = '/dev/' + port_name
                    print(f'using device {self.config.device_name}')
        self.portHandler = PortHandler(self.config.device_name)
        # self.portHandler.LA
        self.packetHandler = PacketHandler(self.config.protocol_version)
        if not self.portHandler.openPort():
            raise Exception(f'Failed to open port {self.config.device_name}')

        if not self.portHandler.setBaudRate(self.config.baudrate):
            raise Exception(f'failed to set baudrate to {self.config.baudrate}')

        # self.operating_mode = OperatingMode.UNKNOWN
        # self.torque_enabled = False
        # self._disable_torque()

        self.operating_modes = [None for _ in range(32)]
        self.torque_enabled = [None for _ in range(32)]
        return True

    def disconnect(self):
        self.portHandler.closePort()

    def set_goal_position(self, motor_id, goal_position):
        # if self.operating_modes[motor_id] is not OperatingMode.POSITION:
        #     self._disable_torque(motor_id)
        #     self.set_operating_mode(motor_id, OperatingMode.POSITION)

        # if not self.torque_enabled[motor_id]:
        #     self._enable_torque(motor_id)

        # self._enable_torque(motor_id)
        dxl_comm_result, dxl_error = self.packetHandler.write4ByteTxRx(self.portHandler, motor_id,
                                                                       self.ADDR_GOAL_POSITION, goal_position)
        # self._process_response(dxl_comm_result, dxl_error)
        # print(f'set position of motor {motor_id} to {goal_position}')

    def set_pwm_value(self, motor_id: int, pwm_value, tries=3):
        if self.operating_modes[motor_id] is not OperatingMode.PWM:
            self._disable_torque(motor_id)
            self.set_operating_mode(motor_id, OperatingMode.PWM)

        if not self.torque_enabled[motor_id]:
            self._enable_torque(motor_id)
            # print(f'enabling torque')
        dxl_comm_result, dxl_error = self.packetHandler.write2ByteTxRx(self.portHandler, motor_id,
                                                                       self.ADDR_GOAL_PWM, pwm_value)
        # self._process_response(dxl_comm_result, dxl_error)
        # print(f'set pwm of motor {motor_id} to {pwm_value}')
        if dxl_comm_result != COMM_SUCCESS:
            if tries <= 1:
                raise ConnectionError(f"dxl_comm_result: {self.packetHandler.getTxRxResult(dxl_comm_result)}")
            else:
                print(f'dynamixel pwm setting failure trying again with {tries - 1} tries')
                self.set_pwm_value(motor_id, pwm_value, tries=tries - 1)
        elif dxl_error != 0:
            print(f'dxl error {dxl_error}')
            raise ConnectionError(f"dynamixel error: {self.packetHandler.getTxRxResult(dxl_error)}")

    def read_temperature(self, motor_id: int):
        return self._read_value(motor_id, ReadAttribute.TEMPERATURE, 1)

    def read_velocity(self, motor_id: int):
        pos = self._read_value(motor_id, ReadAttribute.VELOCITY, 4)
        if pos > 2 ** 31:
            pos -= 2 ** 32
        # print(f'read position {pos} for motor {motor_id}')
        return pos

    def read_position(self, motor_id: int):
        pos = self._read_value(motor_id, ReadAttribute.POSITION, 4)
        if pos > 2 ** 31:
            pos -= 2 ** 32
        # print(f'read position {pos} for motor {motor_id}')
        return pos

    def read_position_degrees(self, motor_id: int) -> float:
        return (self.read_position(motor_id) / 4096) * 360

    def read_position_radians(self, motor_id: int) -> float:
        return (self.read_position(motor_id) / 4096) * 2 * math.pi

    def read_current(self, motor_id: int):
        current = self._read_value(motor_id, ReadAttribute.CURRENT, 2)
        if current > 2 ** 15:
            current -= 2 ** 16
        return current

    def read_present_pwm(self, motor_id: int):
        return self._read_value(motor_id, ReadAttribute.PWM, 2)

    def read_hardware_error_status(self, motor_id: int):
        return self._read_value(motor_id, ReadAttribute.HARDWARE_ERROR_STATUS, 1)

    def disconnect(self):
        self.portHandler.closePort()

    def set_id(self, old_id, new_id, use_broadcast_id: bool = False):
        """
        sets the id of the dynamixel servo
        @param old_id: current id of the servo
        @param new_id: new id
        @param use_broadcast_id: set ids of all connected dynamixels if True.
         If False, change only servo with self.config.id
        @return:
        """
        if use_broadcast_id:
            current_id = 254
        else:
            current_id = old_id
        dxl_comm_result, dxl_error = self.packetHandler.write1ByteTxRx(self.portHandler,
                                                                       current_id, self.ADDR_ID, new_id)
        self._process_response(dxl_comm_result, dxl_error, old_id)
        self.config.id = id

    def _enable_torque(self, motor_id):
        dxl_comm_result, dxl_error = self.packetHandler.write1ByteTxRx(self.portHandler, motor_id,
                                                                       self.ADDR_TORQUE_ENABLE, 1)
        self._process_response(dxl_comm_result, dxl_error, motor_id)
        self.torque_enabled[motor_id] = True

    def _disable_torque(self, motor_id):
        dxl_comm_result, dxl_error = self.packetHandler.write1ByteTxRx(self.portHandler, motor_id,
                                                                       self.ADDR_TORQUE_ENABLE, 0)
        self._process_response(dxl_comm_result, dxl_error, motor_id)
        self.torque_enabled[motor_id] = False

    def _process_response(self, dxl_comm_result: int, dxl_error: int, motor_id: int):
        if dxl_comm_result != COMM_SUCCESS:
            raise ConnectionError(
                f"dxl_comm_result for motor {motor_id}: {self.packetHandler.getTxRxResult(dxl_comm_result)}")
        elif dxl_error != 0:
            print(f'dxl error {dxl_error}')
            raise ConnectionError(
                f"dynamixel error for motor {motor_id}: {self.packetHandler.getTxRxResult(dxl_error)}")

    def set_operating_mode(self, motor_id: int, operating_mode: OperatingMode):
        dxl_comm_result, dxl_error = self.packetHandler.write2ByteTxRx(self.portHandler, motor_id,
                                                                       self.OPERATING_MODE_ADDR, operating_mode.value)
        self._process_response(dxl_comm_result, dxl_error, motor_id)
        self.operating_modes[motor_id] = operating_mode

    def set_pwm_limit(self, motor_id: int, limit: int):
        dxl_comm_result, dxl_error = self.packetHandler.write2ByteTxRx(self.portHandler, motor_id,
                                                                       36, limit)
        self._process_response(dxl_comm_result, dxl_error, motor_id)

    def set_velocity_limit(self, motor_id: int, velocity_limit):
        dxl_comm_result, dxl_error = self.packetHandler.write4ByteTxRx(self.portHandler, motor_id,
                                                                       self.ADDR_VELOCITY_LIMIT, velocity_limit)
        self._process_response(dxl_comm_result, dxl_error, motor_id)

    def set_P(self, motor_id: int, P: int):
        dxl_comm_result, dxl_error = self.packetHandler.write2ByteTxRx(self.portHandler, motor_id,
                                                                       self.POSITION_P, P)
        self._process_response(dxl_comm_result, dxl_error, motor_id)

    def set_I(self, motor_id: int, I: int):
        dxl_comm_result, dxl_error = self.packetHandler.write2ByteTxRx(self.portHandler, motor_id,
                                                                       self.POSITION_I, I)
        self._process_response(dxl_comm_result, dxl_error, motor_id)

    def read_home_offset(self, motor_id: int):
        self._disable_torque(motor_id)
        # dxl_comm_result, dxl_error = self.packetHandler.write4ByteTxRx(self.portHandler, motor_id,
        #                                                                ReadAttribute.HOMING_OFFSET.value, home_position)
        home_offset = self._read_value(motor_id, ReadAttribute.HOMING_OFFSET, 4)
        # self._process_response(dxl_comm_result, dxl_error)
        self._enable_torque(motor_id)
        return home_offset

    def set_home_offset(self, motor_id: int, home_position: int):
        self._disable_torque(motor_id)
        dxl_comm_result, dxl_error = self.packetHandler.write4ByteTxRx(self.portHandler, motor_id,
                                                                       ReadAttribute.HOMING_OFFSET.value, home_position)
        self._process_response(dxl_comm_result, dxl_error, motor_id)
        self._enable_torque(motor_id)

    def set_baudrate(self, motor_id: int, baudrate):
        # translate baudrate into dynamixel baudrate setting id
        if baudrate == 57600:
            baudrate_id = 1
        elif baudrate == 1_000_000:
            baudrate_id = 3
        elif baudrate == 2_000_000:
            baudrate_id = 4
        elif baudrate == 3_000_000:
            baudrate_id = 5
        elif baudrate == 4_000_000:
            baudrate_id = 6
        else:
            raise Exception('baudrate not implemented')

        self._disable_torque(motor_id)
        dxl_comm_result, dxl_error = self.packetHandler.write1ByteTxRx(self.portHandler, motor_id,
                                                                       ReadAttribute.BAUDRATE.value, baudrate_id)
        self._process_response(dxl_comm_result, dxl_error, motor_id)

    def _read_value(self, motor_id, attribute: ReadAttribute, num_bytes: int, tries=10):
        try:
            if num_bytes == 1:
                value, dxl_comm_result, dxl_error = self.packetHandler.read1ByteTxRx(self.portHandler,
                                                                                     motor_id,
                                                                                     attribute.value)
            elif num_bytes == 2:
                value, dxl_comm_result, dxl_error = self.packetHandler.read2ByteTxRx(self.portHandler,
                                                                                     motor_id,
                                                                                     attribute.value)
            elif num_bytes == 4:
                value, dxl_comm_result, dxl_error = self.packetHandler.read4ByteTxRx(self.portHandler,
                                                                                     motor_id,
                                                                                     attribute.value)
        except Exception:
            if tries == 0:
                raise Exception
            else:
                return self._read_value(motor_id, attribute, num_bytes, tries=tries - 1)
        if dxl_comm_result != COMM_SUCCESS:
            if tries <= 1:
                # print("%s" % self.packetHandler.getTxRxResult(dxl_comm_result))
                raise ConnectionError(f'dxl_comm_result {dxl_comm_result} for servo {motor_id} value {value}')
            else:
                print(f'dynamixel read failure for servo {motor_id} trying again with {tries - 1} tries')
                time.sleep(0.02)
                return self._read_value(motor_id, attribute, num_bytes, tries=tries - 1)
        elif dxl_error != 0:  # # print("%s" % self.packetHandler.getRxPacketError(dxl_error))
            # raise ConnectionError(f'dxl_error {dxl_error} binary ' + "{0:b}".format(37))
            if tries == 0 and dxl_error != 128:
                raise Exception(f'Failed to read value from motor {motor_id} error is {dxl_error}')
            else:
                return self._read_value(motor_id, attribute, num_bytes, tries=tries - 1)
        return value

    def set_home_position(self, motor_id: int):
        print(f'setting home position for motor {motor_id}')
        self.set_home_offset(motor_id, 0)
        current_position = self.read_position(motor_id)
        print(f'position before {current_position}')
        self.set_home_offset(motor_id, -current_position)
        # dynamixel.set_home_offset(motor_id, -4096)
        # dynamixel.set_home_offset(motor_id, -4294964109)
        current_position = self.read_position(motor_id)
        # print(f'signed position {current_position - 2** 32}')
        print(f'position after {current_position}')


if __name__ == "__main__":
    dynamixel = Dynamixel.Config(
        baudrate=1_000_000,
        device_name='/dev/tty.usbmodem57380045631'
    ).instantiate()
    motor_id = 1
    pos = dynamixel.read_position(motor_id)
    for i in range(10):
        s = time.monotonic()
        pos = dynamixel.read_position(motor_id)
        delta = time.monotonic() - s
        print(f'read position took {delta}')
        print(f'position {pos}')

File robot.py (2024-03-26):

import numpy as np
from dynamixel import Dynamixel, OperatingMode, ReadAttribute
import time
from dynamixel_sdk import GroupSyncRead, GroupSyncWrite, DXL_LOBYTE, DXL_HIBYTE, DXL_LOWORD, DXL_HIWORD
from enum import Enum, auto
from typing import Union


class MotorControlType(Enum):
    PWM = auto()
    POSITION_CONTROL = auto()
    DISABLED = auto()
    UNKNOWN = auto()


class Robot:
    # def __init__(self, device_name: str, baudrate=1_000_000, servo_ids=[1, 2, 3, 4, 5]):
    def __init__(self, dynamixel, baudrate=1_000_000, servo_ids=[1, 2, 3, 4, 5]):
        self.servo_ids = servo_ids
        self.dynamixel = dynamixel
        # self.dynamixel = Dynamixel.Config(baudrate=baudrate, device_name=device_name).instantiate()
        self.position_reader = GroupSyncRead(
            self.dynamixel.portHandler,
            self.dynamixel.packetHandler,
            ReadAttribute.POSITION.value,
            4)
        for id in self.servo_ids:
            self.position_reader.addParam(id)

        self.velocity_reader = GroupSyncRead(
            self.dynamixel.portHandler,
            self.dynamixel.packetHandler,
            ReadAttribute.VELOCITY.value,
            4)
        for id in self.servo_ids:
            self.velocity_reader.addParam(id)

        self.pos_writer = GroupSyncWrite(
            self.dynamixel.portHandler,
            self.dynamixel.packetHandler,
            self.dynamixel.ADDR_GOAL_POSITION,
            4)
        for id in self.servo_ids:
            self.pos_writer.addParam(id, [2048])

        self.pwm_writer = GroupSyncWrite(
            self.dynamixel.portHandler,
            self.dynamixel.packetHandler,
            self.dynamixel.ADDR_GOAL_PWM,
            2)
        for id in self.servo_ids:
            self.pwm_writer.addParam(id, [2048])
        self._disable_torque()
        self.motor_control_state = MotorControlType.DISABLED

    def read_position(self, tries=2):
        """
        Reads the joint positions of the robot. 2048 is the center position. 0 and 4096 are 180 degrees in each direction.
        :param tries: maximum number of tries to read the position
        :return: list of joint positions in range [0, 4096]
        """
        result = self.position_reader.txRxPacket()
        if result != 0:
            if tries > 0:
                return self.read_position(tries=tries - 1)
            else:
                print(f'failed to read position!!!!!!!!!!!!!!!!!!!!!!!!!!!!!')
        positions = []
        for id in self.servo_ids:
            position = self.position_reader.getData(id, ReadAttribute.POSITION.value, 4)
            if position > 2 ** 31:
                position -= 2 ** 32
            positions.append(position)
        return positions

    def read_velocity(self):
        """
        Reads the joint velocities of the robot.
        :return: list of joint velocities,
        """
        self.velocity_reader.txRxPacket()
        velocties = []
        for id in self.servo_ids:
            velocity = self.velocity_reader.getData(id, ReadAttribute.VELOCITY.value, 4)
            if velocity > 2 ** 31:
                velocity -= 2 ** 32
            velocties.append(velocity)
        return velocties

    def set_goal_pos(self, action):
        """

        :param action: list or numpy array of target joint positions in range [0, 4096]
        """
        if not self.motor_control_state is MotorControlType.POSITION_CONTROL:
            self._set_position_control()
        for i, motor_id in enumerate(self.servo_ids):
            data_write = [DXL_LOBYTE(DXL_LOWORD(action[i])),
                          DXL_HIBYTE(DXL_LOWORD(action[i])),
                          DXL_LOBYTE(DXL_HIWORD(action[i])),
                          DXL_HIBYTE(DXL_HIWORD(action[i]))]
            self.pos_writer.changeParam(motor_id, data_write)

        self.pos_writer.txPacket()

    def set_pwm(self, action):
        """
        Sets the pwm values for the servos.
        :param action: list or numpy array of pwm values in range [0, 885]
        """
        if not self.motor_control_state is MotorControlType.PWM:
            self._set_pwm_control()
        for i, motor_id in enumerate(self.servo_ids):
            data_write = [DXL_LOBYTE(DXL_LOWORD(action[i])),
                          DXL_HIBYTE(DXL_LOWORD(action[i])),
                          ]
            self.pwm_writer.changeParam(motor_id, data_write)

        self.pwm_writer.txPacket()

    def set_trigger_torque(self):
        """
        Sets a constant torque torque for the last servo in the chain. This is useful for the trigger of the leader arm
        """
        self.dynamixel._enable_torque(self.servo_ids[-1])
        self.dynamixel.set_pwm_value(self.servo_ids[-1], 200)

    def limit_pwm(self, limit: Union[int, list, np.ndarray]):
        """
        Limits the pwm values for the servos in for position control
        @param limit: 0 ~ 885
        @return:
        """
        if isinstance(limit, int):
            limits = [limit, ] * 5
        else:
            limits = limit
        self._disable_torque()
        for motor_id, limit in zip(self.servo_ids, limits):
            self.dynamixel.set_pwm_limit(motor_id, limit)
        self._enable_torque()

    def _disable_torque(self):
        print(f'disabling torque for servos {self.servo_ids}')
        for motor_id in self.servo_ids:
            self.dynamixel._disable_torque(motor_id)

    def _enable_torque(self):
        print(f'enabling torque for servos {self.servo_ids}')
        for motor_id in self.servo_ids:
            self.dynamixel._enable_torque(motor_id)

    def _set_pwm_control(self):
        self._disable_torque()
        for motor_id in self.servo_ids:
            self.dynamixel.set_operating_mode(motor_id, OperatingMode.PWM)
        self._enable_torque()
        self.motor_control_state = MotorControlType.PWM

    def _set_position_control(self):
        self._disable_torque()
        for motor_id in self.servo_ids:
            self.dynamixel.set_operating_mode(motor_id, OperatingMode.POSITION)
        self._enable_torque()
        self.motor_control_state = MotorControlType.POSITION_CONTROL


if __name__ == "__main__":
    robot = Robot(device_name='/dev/tty.usbmodem57380045631')
    robot._disable_torque()
    for _ in range(10000):
        s = time.time()
        pos = robot.read_position()
        elapsed = time.time() - s
        print(f'read took {elapsed} pos {pos}')

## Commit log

2024-03-23 Upload 3D design files and add simple control program
    [arm.step, base.step, elbow_to_wrist.step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]
2024-03-23 add robot arm picture
2024-03-23 add stl files
    [arm.step, base.step, base.stl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]
2024-03-24 fix servo name
2024-03-24 add base
    [base.stl]
2024-03-25 update leader gripper trigger design for large open angle and smoother design
    [gripper_trigger.step, gripper_trigger.stl]
2024-03-26 Add elbow to wrist expansion for a total of 5DoF + gripper
    [elbow_to_wrist_extension.step, elbow_to_wrist_extension.stl]
2024-04-03 update sliced 3D print files
2024-04-03 typo in naming
    [shoulder_to_elbow.step, shoulder_to_elbow.stl]
2024-04-10 Resolve conflict between Dynamixel item name, buying link, and specs
    Change the first part of the leader arm required materials from XL330-W077 to XL330-M077.
    This is because the buying link and specs columns provided correspond to XL330-M077,
    but the text in the Part column was XL330-W077.
2024-04-11 add teleoperation for simulated robot arm
    [low_cost_robot.xml]
2024-05-24 add extra axis to arm design files
    [arm.step]
2024-05-24 add extra axis to leader arm
    [leader_arm.step]
2024-05-24 update CAD pictures
